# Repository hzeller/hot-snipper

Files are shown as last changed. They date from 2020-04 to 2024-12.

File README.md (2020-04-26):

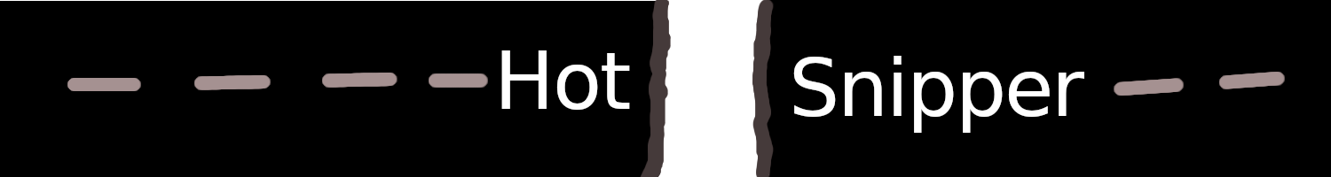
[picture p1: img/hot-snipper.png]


# Hot Knife cutting machine for synthetic button-hole bands

*Work in Progress*

Here at [MakerNexus], we're now producing the [Covid-19 effort][FaceShields]
face-shield parts via injection-molding, so now one bottleneck is to cut
enough elastic bands, which at this point happens entirely by hand.

This device helps to cut button-hole elastic.

It is specialized to work with the particular band we have in width
and button-hole distance; it cuts exactly the length we need (18 holes apart,
just between the holes). Changes in these specifications can easily be
adapted with the parametric CAD model.

This machine is for that, a hot knife (really at this point: hot wire) cutter
that allows to cut multiple parallel bands at once.

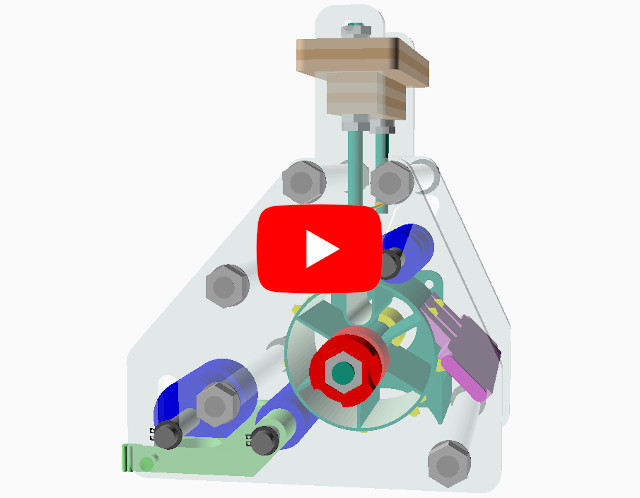
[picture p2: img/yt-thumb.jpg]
(https://www.youtube.com/watch?v=Wu0xrwdAlOw "Animation")


## Manufacturing
Most items can be entirely 3D printed, the side panels and wooden handle
is laser cut. To generate manufacturing outputs with OpenSCAD, type `make`.

### 3D printing
The provided fab/band-cutter-machine.3mf file contains a print layout that
provides all the parts needed to print a machine that can cut two bands in
parallel (This fits on an area small enough to be printed on a Prusa Mini).

#### Changing parallel bands
By default, the stack of bands that is cut in parallel is two, but that
can be changed with a parameter. A machine that can cut up to 5 bands in
parallel can fit on a Prusa MK3 bed.

```bash
make BAND_STACK=5  # to build the new artifacts; here we want 5 bands
cd fab/            # because prusa-slicer 3MF does not handle relative paths...
prusa-slicer band-cutter-machine.3mf
# Now, press F5 in the UI for reload.
```

There seems to be a bug in prusa-slicer which then slightly mis-aligns the
cylinder support enforcer around the main wheel; adjust that first before
slicing.

 Two band wide                      | Five band wide
------------------------------------|------------------------------------
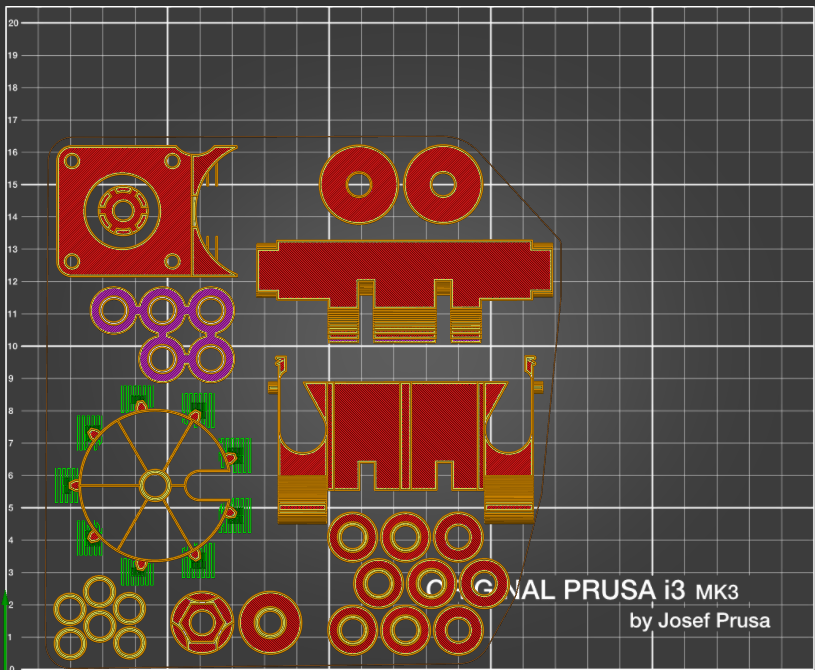
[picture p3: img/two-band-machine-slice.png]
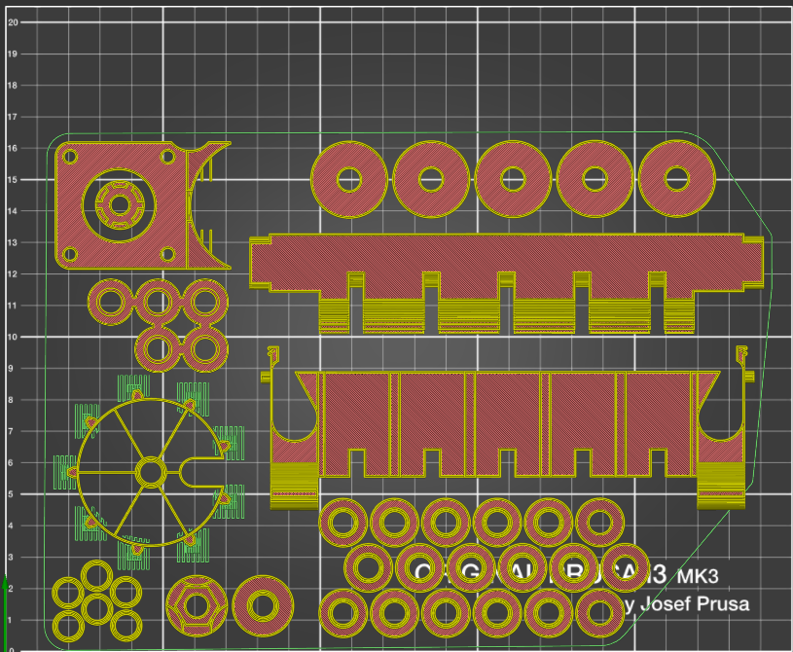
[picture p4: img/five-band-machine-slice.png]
 | 

The side-panels take a lot of time to print, so we laser-cut these (but
you can also print `fab/mount_panel.stl` if in a pinch and don't have access
to a laser cutter).

### Laser Cutting

There are two files, provided as DXF format that need to be laser-cut.

  * `fab/laser_cut_knife_slider.dxf` Needs to be cut from 3mm plywood.
  * `fab/laser_cut_mount_panel.dxf` can be wood, but ideally transparent
    acrylic to inspect the inside of the machine.

 Knife Slider (plywood, 3mm)        | Mount Panel (acrylic, 6mm)
------------------------------------|------------------------------------
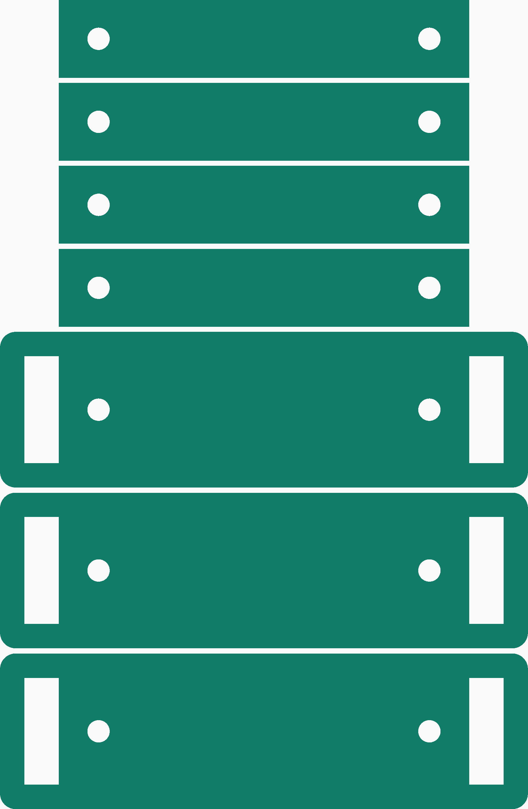
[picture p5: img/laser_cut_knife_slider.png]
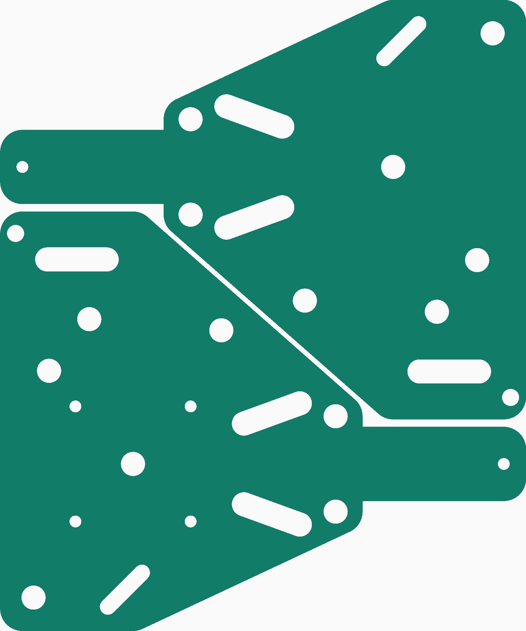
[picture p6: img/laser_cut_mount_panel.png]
 | 

## Assembly

Parts fit together pretty straightforward, check out the rendering and
picture below. Note that the spacing tubes for the axles come in two sizes:
the ones around the in-feed idler with the big wheels are slightly longer than
the other idler axes.

As 'axles', I am using easy-to-get threaded rods, cut to length (whatever
is easy to get; 6mm or 1/4").
All idler-axles should be held in place by retaining rings (I don't have any
right now, so this is why it is temporarily using nuts).

The center wheel is driven by a stepper motor, mounted on one side of the
panel. There is a meshing coupler that drives the wheel. Since the motor
axle is not long enough to go all the way through the machine, there is a
floating axle on the opposing side that is mounted firmly perpendicular to
the panel with flat nuts with a large surface.

The hot wire is mounted between two threaded rods (#8, about 4.2mm), held
apart by a wooden block made up of a couple of layers laser-cut plywood. That
way, that part does not soften over time near the rods that get warm in
operation.

Put aluminum sticky tape inside the wheel channel.

 Render                     | Assembled (older model)
----------------------------|-----------------------
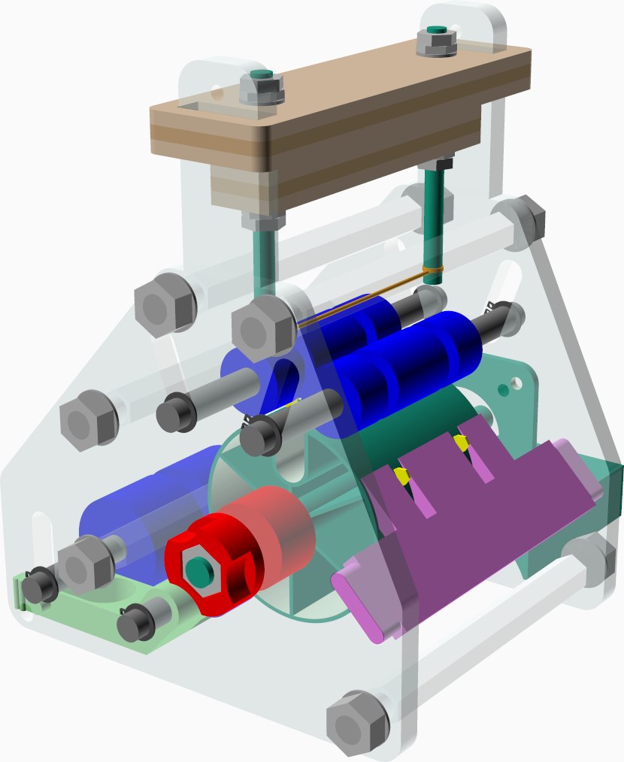
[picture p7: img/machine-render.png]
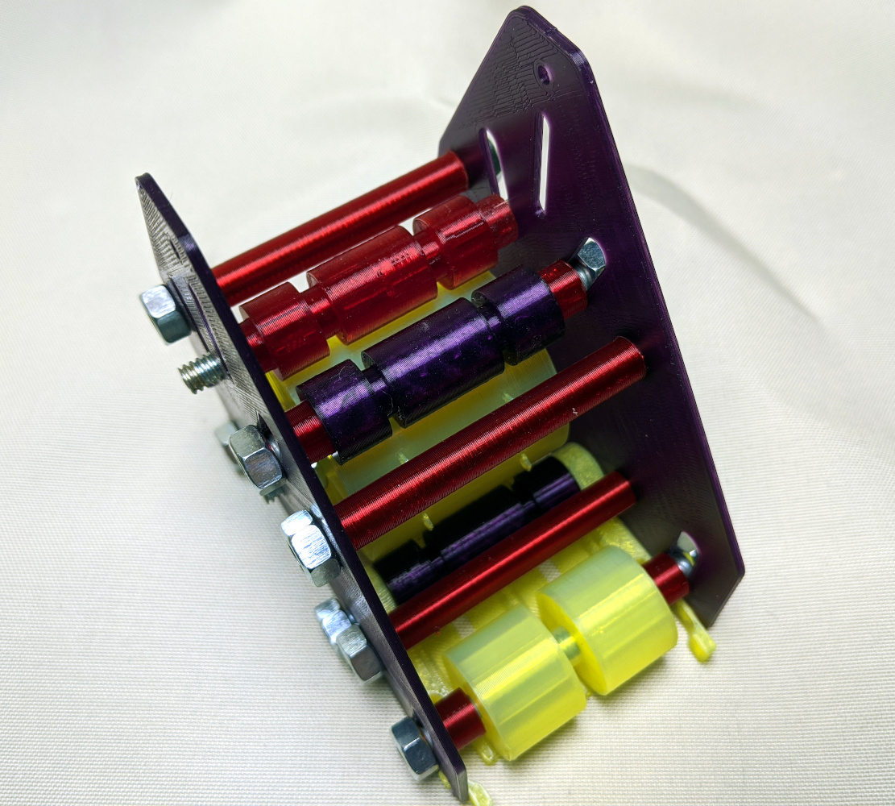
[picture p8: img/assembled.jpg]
 | 

## Usage

Loading the band requires it to go around the lower idler, then around the
central wheel and emerging at the top.

In order to get it through the in-feed tray and under the lower idler, it
is possible to unlatch the infeed-tray and rotate so that this can be done
with the least amount of fiddling.

 Feeding with opened loading tray        | Closed back up
-----------------------------------------|----------------
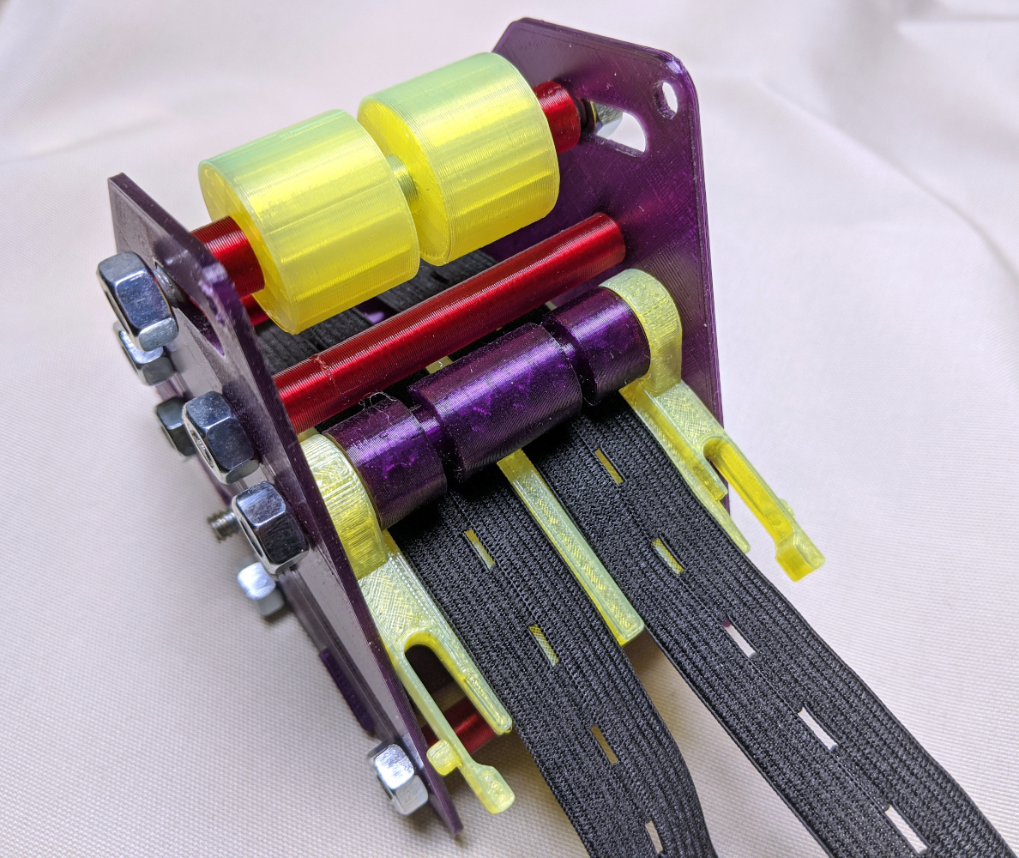
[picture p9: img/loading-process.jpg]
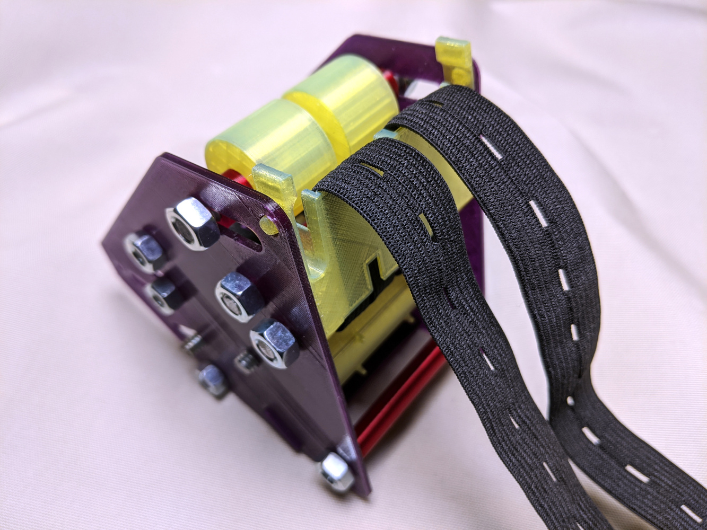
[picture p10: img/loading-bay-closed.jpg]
             | 

Now, wrap around the button elastic half way around the big wheel, then
under the top idlers (that can be moved up manually. In this picture purple
and red) so that the elastics emerge at the front; we're now fully loaded:

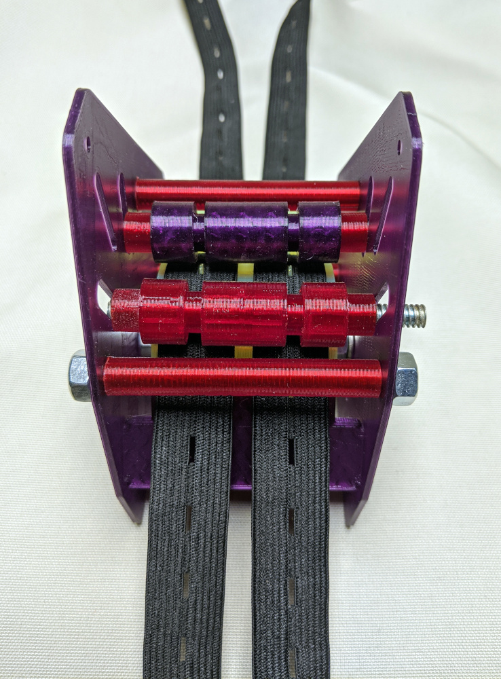
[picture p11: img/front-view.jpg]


### License

This is shared with the Creative Commons Attribution-ShareAlike [CC-BY-SA]
license.

[MakerNexus]: https://makernexus.com/
[FaceShields]: https://www.covidshieldnexus.org/
[CC-BY-SA]: https://creativecommons.org/licenses/by-sa/4.0/

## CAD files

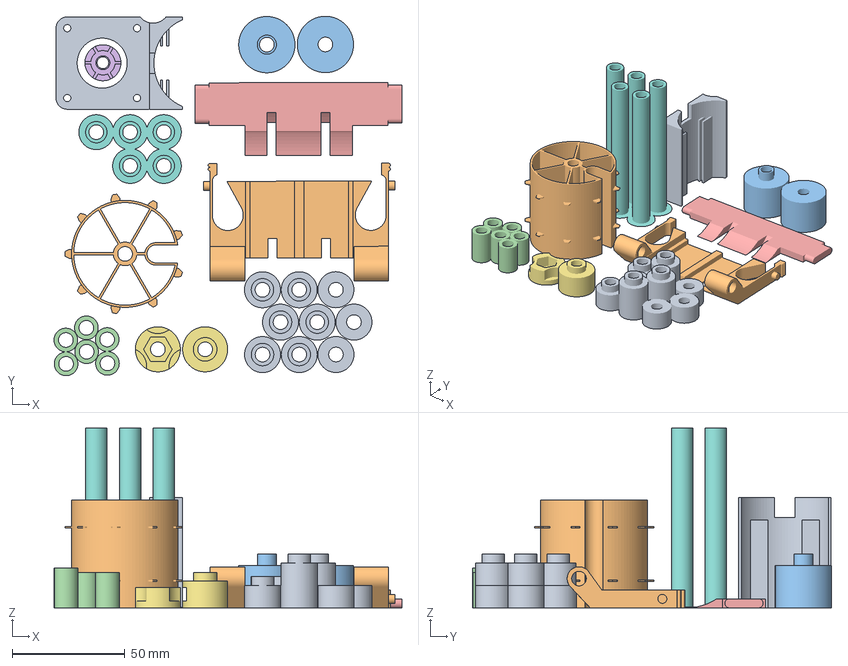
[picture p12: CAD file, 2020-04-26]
fab/band-cutter-machine.3mf
154.5 x 159.6 x 79.8 mm
print_wheel_idler.stl
infeed_fancy_tray.stl
print_infeed_weight_idler.stl
print_sidewall_clearance_distance_rings.stl
print_outfeed.stl
motor_coupler.stl
print_motor_bearing_parts.stl
print_stack_spacer.stl
print_nema_motor_stand.stl
wheel_stack.stl

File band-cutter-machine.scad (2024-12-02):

// -*- mode: scad; c-basic-offset: 2; indent-tabs-mode: nil; -*-
// (c) 2020 Henner Zeller <h.zeller@acm.org>
//
// This file is provided under the license condition of Creative Commons BY-SA
// https://creativecommons.org/licenses/by-sa/4.0/

use <utils.scad>

$fn=120;
e=0.01;
PI=3.1415926536;

stack=2;

// In one animation, we go through a few cycles, as we move camera positions,
// see camera_position() function.
anim_t=5*$t % 1;

// The phases we animate the knife and rotation.
anim_knife_range = [0, 0.6];  // first 60% of the time.
anim_rot_range = [0.6, 1];

//button_hole_distance=25.4 / 1.5;  // theoretical..
button_hole_distance=564 / 34;      // measured ...
hole_count=18;   // This determines the length of the final band. Must be even.

band_separation=4.1;               // How far apart we have the bands
baseline_band=19.8;                // Elastic band width.
band_thick=baseline_band + band_separation;  // Actual width + separation.

side_wall_clearance=16;           // Clearance mostly for the hot wire.
axle_dia=6.5;   // 1/4" rod + extra; we use that for all axles, main and idlers
axle_hex_flat_size=11;  // hex nut for above.
axle_hex_thick=6;

bands_per_wheel=0.5;
cut_slot_deep=10;

axle_display=axle_dia;
spoke_angle=60;

// Main wheel parameters
wheel_wall=1;
spoke_thick=1;
spoke_slot=4;

hole_angle=360/(bands_per_wheel*hole_count);
circ=bands_per_wheel * hole_count * button_hole_distance;
radius=circ / (2*PI);

idler_dia=16;
idler_cutout=4;
infeed_idler_dia=25;

knife_movement=25;     // Total vertical movement

stack_spacer_wall=1.5;       // od vs. id for stack spacer tubes.
stack_spacer_rod_dia=axle_dia;
stack_spacer_print_flat=true;   // make hexagon instead of round.

// the part engaging with the frame. This is multiple of 3mm as cut from
// plywood.
knife_slide_layers=7;
knife_slide_top_layers=3;
knife_slide_layer_thick=3;
knife_slide_len=knife_slide_layers * knife_slide_layer_thick;
knife_slide_top_len=knife_slide_top_layers * knife_slide_layer_thick;
knife_slide_rod_hole=4.3;   // The diameter threaded rod holding the wire.

knife_slider_above_wire=30;
knife_into_wheel=4;   // How deep we go into the slot. Mostly for animation
knife_slider_slot_w=20;
knife_slider_ring_support=5;       // Ring that wraps around slide dagger
knife_slider_bottom_block_w=15;    // Needs to support at least the nut diameter

fit_tolerance=0.3;                 // Tolerance of parts in contact.
slide_tolerance=fit_tolerance;     // Tolerance of parts sliding
rotation_clearance=fit_tolerance;  // Similar for rotational

infeed_tray_high=4;
outfeed_offset=0.65;       // Wheel to outfeed wedge.

nema_cutout=false;   // should we have a central cut-out for the nema17?

mount_panel_thickness=6;  // thickness of material for the frame, e.g. acrylic.
mount_panel_corner_r=6;

// Blades engaging with the button-holes
blade_h=3.5;
blade_w=0.7;
blade_l=4;

top_knife_pos = radius - knife_into_wheel
  + knife_slider_above_wire
  + (knife_slide_layers-knife_slide_top_layers)*knife_slide_layer_thick;

mount_hole_flush_with_top_knife
= top_knife_pos - axle_dia/2-stack_spacer_wall
  - 2.5;  // To accomodate washer and nut.
panel_corner_flush_with_top_knife = top_knife_pos - mount_panel_corner_r;

mount_hole_next_to_knife_block = knife_slider_bottom_block_w/2
  + stack_spacer_wall + stack_spacer_rod_dia/2
  + 2*slide_tolerance;  // a bit more than usual because we dive into it.

// Places where we add spacers to rigidly hold together the two side-frames.
mount_holes
 = [[39, -radius+12], [36, radius],  // Infeed side
    [-36, -radius-3],                // Outfeed side
    // Top around knife slider.
    [mount_hole_next_to_knife_block, mount_hole_flush_with_top_knife],
    [-mount_hole_next_to_knife_block, mount_hole_flush_with_top_knife]];

mount_panel_corners
 = [[-39, -radius - 6],         // bottom, out-feed side
    [-39, 0], //[-30, +radius+idler_dia], // up out-feed side.
    [-mount_hole_next_to_knife_block, panel_corner_flush_with_top_knife],
    [mount_hole_next_to_knife_block, panel_corner_flush_with_top_knife], // summit
    [62, 0], [62, -radius - 6]];  // down, in-feed

echo("circumreference ", circ, "; radius=", radius, "; teeth=", bands_per_wheel*hole_count, "; inner-width: ", stack * band_thick + 2*side_wall_clearance, "; knife-rod-distance: ", stack * band_thick + side_wall_clearance);

// Some colors used below
color_tooth="yellow";
color_knife="orange";   // glow
color_wheel_idler="blue";
color_axle="gray";
color_infeed="lightgreen";
color_outfeed="violet";
color_panel=[1, 1, 1, 0.1];
color_stack_spacer=[0, 1, 0, 0.25];
color_motor_coupler="yellow";
color_counter_bearing="red";
color_wood=["#d8c0a3", "#c9a77e"];  // plywood 'wood' layers

module mount_place(dia) {
  translate([0, 0, -band_thick/2]) cylinder(r=dia/2 + 2, h=band_thick);
}

module mount_place_punch(dia) {
  translate([0, 0, -(band_thick+e)/2]) cylinder(r=dia/2, h=band_thick+2*e);
}

// A 'tooth' engaging with a button hole.
module button_hole_tooth() {
  color(color_tooth) hull() {
    cube([e, blade_l, blade_w], center=true);
    translate([1.5, 0, 0]) cube([e, blade_l, blade_w], center=true);
    translate([blade_h, 0, 0]) cube([e, blade_l-2, blade_w], center=true);
  }
}

// Widening to accomodate hot knife through wheel.
module spoke_cut_widening(from_edge=cut_slot_deep) {
  widening_r=spoke_slot + spoke_thick;
  translate([radius - from_edge, 0, -band_thick/2]) hull() {
    cylinder(r=widening_r, h=band_thick);
    translate([from_edge, -widening_r, 0]) cube([e, 2*widening_r, band_thick]);
  }
}

module spoke_cut_widening_punch(from_edge=cut_slot_deep) {
  cutout_h=band_thick+2*e;
  translate([radius-from_edge, 0, -cutout_h/2]) hull() {
    cylinder(r=spoke_slot, h=cutout_h);
    translate([from_edge, -spoke_slot, 0]) cube([e, 2*spoke_slot, cutout_h]);
  }
}

module basic_wheel(extra=0) {
  // Outer cylinder, hollowed
  translate([0, 0, -band_thick/2]) difference() {
    cylinder(r=radius, h=band_thick);
    translate([0, 0, -e]) cylinder(r=radius-wheel_wall, h=band_thick+2*e);
  }

  // spokes.
  intersection() {
    union() {
      for (a=[0:spoke_angle:360]) {
        rotate([0, 0, a]) {
          translate([radius/2, 0, 0]) cube([radius, spoke_thick+extra, band_thick], center=true);
        }
      }
      spoke_cut_widening();
    }

    translate([0, 0, -band_thick/2]) cylinder(r=radius, h=band_thick);
  }

  mount_place(dia=axle_dia+extra);  // axle in center
}

module wheel_assembly(extra=0) {
  difference() {
    basic_wheel(extra);
    spoke_cut_widening_punch();
    mount_place_punch(dia=axle_dia-extra);
  }

  for (a=[hole_angle/2:hole_angle:360-e]) {
    rotate([0, 0, a]) translate([radius-0.5, 0, 0]) button_hole_tooth();
  }
}

module wheel_stack(layers=stack, with_axle=false) {
  d=band_thick;
  axle_extra=side_wall_clearance+mount_panel_thickness + 10;
  for (i = [0:1:layers-e]) {
    translate([0, 0, i*d]) wheel_assembly();
  }

  if (with_axle) {
    // TODO: add motor mount thing and counter-nut.
    translate([0, 0, -band_thick/2-axle_extra]) cylinder(r=axle_dia/2, h=layers*band_thick+2*axle_extra);
  }
}

// The knife is mostly non-3D printed, but made out of other materials
//  * the wire itself out of nichrome
//  * the connecting columns are some threaded rod.
module knife(s=stack) {
  d=band_thick;
  nd=8;   // nut dia
  nh=2.5; // nut height
  translate([-d/2, -0, 0]) {
    translate([-side_wall_clearance/2, 0, 0]) rotate([0, 90, 0]) color(color_knife)
      cylinder(r=0.5, h=s*d+side_wall_clearance);  // 'wire'

    translate([-side_wall_clearance/2, 0, 0]) {
      translate([0, 0, -3]) cylinder(r=4.5/2, h=60);  // rod
      color(color_knife) cylinder(r=5/2, h=1);
      translate([0, 0, knife_slider_above_wire-nh]) hex_nut(flat_dia=nd, h=nh);
      translate([0, 0, knife_slider_above_wire-2*nh]) rotate([0, 0, 17]) hex_nut(flat_dia=nd, h=nh); // counter nut.
      translate([0, 0, knife_slider_above_wire+knife_slide_len]) hex_nut(flat_dia=nd, h=nh, with_washer=true);
      translate([0, 0, knife_slider_above_wire+knife_slide_len+nh]) rotate([0, 0, 28]) hex_nut(flat_dia=nd, h=nh);
    }
    translate([s*d+side_wall_clearance/2, 0, 0]) {
      translate([0, 0, -3]) cylinder(r=4.5/2, h=60);
      color(color_knife) cylinder(r=5/2, h=1);
      translate([0, 0, knife_slider_above_wire-nh]) hex_nut(flat_dia=nd, h=nh);
      translate([0, 0, knife_slider_above_wire-2*nh]) rotate([0, 0, 38]) hex_nut(flat_dia=nd, h=nh); // counter nut.
      translate([0, 0, knife_slider_above_wire+knife_slide_len]) hex_nut(flat_dia=nd, h=nh, with_washer=true);
      translate([0, 0, knife_slider_above_wire+knife_slide_len+nh]) rotate([0, 0, 19]) hex_nut(flat_dia=nd, h=nh);
    }
    translate([0, 0, knife_slider_above_wire]) knife_slider();
  }
}
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

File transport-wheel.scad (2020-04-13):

// -*- mode: scad; c-basic-offset: 2; indent-tabs-mode: nil; -*-

$fn=96;
e=0.02;

PI=3.1415926536;

tray_idler_dia=20;

stack=2;
bands_per_wheel=0.5;
cut_slot_deep=10;
axle_dia=6.5;   // 1/4" rod + extra
axle_display=axle_dia - 0.5;
mount_hole_dia=4.5;
mount_hole_pos=5;  // from outside
spoke_angle=60;
do_screws=false;
do_spokes=true;
knife_idler_axle=5;

wheel_wall=1;
spoke_thick=1;

band_separation=1;
band_thick=19.5 + band_separation;
//band_center_thick=12;
band_center_thick=band_thick;


side_wall_clearance=6.95;

hole_count=18;   // This determines the length
hole_angle=360/(bands_per_wheel*hole_count);

//button_hole_distance=286/17;  // measured mm / hole count.
//button_hole_distance=594/35;  // measured mm / hole count.
button_hole_distance=25.4 / 1.5;  // probably actual value.
circ=bands_per_wheel * hole_count * button_hole_distance;
radius=circ / (2*PI);

blade_h=3.5;
blade_w=0.9;
blade_l=5;

mount_holes = [[-30, -radius-2], [30, -radius-2],
	       [30, radius+10], [-28, radius+5]];

echo("circumreference ", circ, "; radius=", radius, "; teeth=", bands_per_wheel*hole_count, "; inner-width: ", stack * band_thick + 2*side_wall_clearance);

module mount_place(dia=mount_hole_dia) {
  translate([0, 0, -band_thick/2]) cylinder(r=dia/2 + 2, h=band_thick);
}

module mount_place_punch(dia=mount_hole_dia) {
  translate([0, 0, -(band_thick+e)/2]) cylinder(r=dia/2, h=band_thick+2*e);
}

module hole_retainer() {
  color("yellow") hull() {
    cube([e, blade_l, blade_w], center=true);
    translate([1.5, 0, 0]) cube([e, blade_l, blade_w], center=true);
    translate([blade_h, 0, 0]) cube([e, blade_l-2, blade_w], center=true);
  }
}

module spoke_cut_widening(from_edge=cut_slot_deep) {
  widening_r=2 + spoke_thick;
  hull() {
    translate([radius - from_edge, 0, -band_thick/2]) cylinder(r=widening_r, h=band_thick);
    if (do_screws) {
      for (a = [-5, 5]) {
        rotate([0, 0, a]) translate([radius-mount_hole_pos, 0, 0]) mount_place();
      }
    } else {
      translate([radius, 0, -band_thick/2]) cylinder(r=widening_r, h=band_thick);
    }
  }
}

module spoke_cut_widening_punch(from_edge=cut_slot_deep) {
  translate([radius-from_edge, 0, -15]) hull() {
    cylinder(r=2, h=30);
    translate([50, 0, 0]) cylinder(r=2, h=30);
  }
}

module basic_wheel() {
  translate([0, 0, -band_center_thick/2]) difference() {
    cylinder(r=radius, h=band_center_thick);
    translate([0, 0, -e]) cylinder(r=radius-wheel_wall, h=band_center_thick+2*e);
  }

  intersection() {
    translate([0, 0, -band_thick/2]) difference() {
      cylinder(r=radius, h=band_thick);
      translate([0, 0, -e]) cylinder(r=radius-wheel_wall, h=band_thick+2*e);
    }
    union() {
      support_arc(0, 30, radius=radius+10, high=band_thick);
      if (bands_per_wheel==2)
        support_arc(180, 30, radius=radius+10, high=band_thick);
    }
  }

  // spokes.
  intersection() {
    union() {
      for (a=[0:spoke_angle:360]) {
        rotate([0, 0, a]) {
          if (do_spokes) translate([radius/2, 0, 0]) cube([radius, spoke_thick, band_center_thick], center=true);
        }
      }

      spoke_cut_widening();

      // Spoke mounts
      if (do_screws) {
        for (a=[spoke_angle:spoke_angle:179]) {
          rotate([0, 0, a]) translate([radius-mount_hole_pos, 0, 0]) mount_place();
          rotate([0, 0, -a]) translate([radius-mount_hole_pos, 0, 0]) mount_place();
        }

        for (a = [-5, 5, 175, 185]) {
          rotate([0, 0, a]) translate([radius-mount_hole_pos, 0, 0]) mount_place();
        }
      }

    }

    translate([0, 0, -band_thick/2]) cylinder(r=radius, h=band_thick);
  }

  if (do_spokes) mount_place(dia=axle_dia);  // axle in center
}

module wheel_assembly() {
  difference() {
    basic_wheel();
    spoke_cut_widening_punch();
    if (do_screws) {
      for (a=[spoke_angle:spoke_angle:179]) {
        rotate([0, 0, a]) translate([radius-mount_hole_pos, 0, 0]) mount_place_punch();
        rotate([0, 0, -a]) translate([radius-mount_hole_pos, 0, 0]) mount_place_punch();
      }
      for (a = [-5, 5, 175, 185]) {
        rotate([0, 0, a]) translate([radius-mount_hole_pos, 0, 0]) mount_place_punch();
      }
    }
    mount_place_punch(dia=axle_dia);
  }

  for (a=[hole_angle/2:hole_angle:360-e]) {
    rotate([0, 0, a]) translate([radius-0.5, 0, 0]) hole_retainer();
  }
}

module stack(layers=3, with_axle=true) {
  d=band_thick;
  axle_extra=side_wall_clearance + 10;
  for (i = [0:1:layers-e]) {
    translate([0, 0, i*d]) wheel_assembly();
  }
  if (with_axle) {
    translate([0, 0, -band_thick/2-axle_extra]) cylinder(r=axle_dia/2, h=layers*band_thick+2*axle_extra);
  }
}

module knife(layers=3, anim_stage=0) {
  movement=15;
  side=0;
  down=sin(anim_stage*180) * movement;
  d=band_thick;
  translate([-side-d/2, -0.5, radius+10-down]) color("red") cube([layers*d+(2*side), 1, 30]);
}

module anim(s=4) {
  t=$t;
  rotate([0, 0, 0]) {
    rotate([180 + ((t < 0.8) ? (t/0.8) * 720 : 0), 0, 0]) rotate([0, 90, 0]) stack(s);
    knife(s, anim_stage = (t > 0.8) ? (t-0.8)/0.2 : 0);

    rotate([90, 0, 180]) rotate([0, -90, 0]) color("darkgray") tangential_band(r=radius, band_wide=band_thick-band_separation-1, in_angle=45, out_angle=135, total_len=500, start_len=481.5-t*button_hole_distance*hole_count);
  }
}

//wheel_assembly();
//stack(1);

module arc_range(start=-10, end=10, radius=100, high=5) {
  hull() {
    cylinder(r=e, h=high);
    rotate([0, 0, start]) translate([radius, 0, 0]) cylinder(r=e, h=high);
    rotate([0, 0, end]) translate([radius, 0, 0]) cylinder(r=e, h=high);
  }
}

module support_arc(center=0, angle_dist=10, radius=100, high=10) {
  small_dist=angle_dist/3;
  hull() {
    translate([0, 0, high/2]) arc_range(start=center-small_dist, end=center+small_dist, radius=radius, high=e);
    arc_range(start=center-angle_dist, end=center+angle_dist, radius=radius, high=e);
    translate([0, 0, -high/2]) arc_range(start=center-small_dist, end=center+small_dist, radius=radius, high=e);
  }
}

//stack(2);

module knife_idler(is_first=false, is_last=false) {
  center_free=3;
  outer=8;
  big_part=(is_first || is_last)
    ? (band_thick-center_free)/2
    : (band_thick-center_free);
  difference() {
    union() {
      cylinder(r=outer, h=big_part);
      if (!is_last) cylinder(r=outer-3, h=big_part+center_free);
    }
    translate([0, 0, -e]) cylinder(r=axle_dia/2, h=band_thick+2*e);
  }
}

module knife_idler_stack(s=5, print_distance=-1, with_axle=false, gravity_holes=false) {
  d = band_thick;
  color("blue") for (i = [0:1:s+1-e]) {
    is_first=(i == 0);
    is_last = (i == s);
    if (print_distance < 0) {
      translate([0, 0, is_first ? 0 : (i-0.5)*d+1.5])
        knife_idler(is_first=is_first, is_last=is_last);
    } else {
      translate([i*print_distance, 0, 0])
        knife_idler(is_first=is_first, is_last=is_last);
    }
  }
  axle_extra=side_wall_clearance + 10;
  if (with_axle) {
    color("gray") translate([0, 0, -axle_extra]) cylinder(r=axle_display/2, h=s*d+2*axle_extra);
  }
  if (gravity_holes) {
    hull() {
      translate([1, 0, -axle_extra]) cylinder(r=axle_dia/2, h=s*d+2*axle_extra);
      translate([-15, 0, -axle_extra]) cylinder(r=axle_dia/2, h=s*d+2*axle_extra);
    }
  }
}

module band_tray(s=5, len=40, extra=0) {
  color("silver") for (i = [0:1:s-e]) {
    translate([i*band_thick, 0, 0]) {
      cube([band_thick, len, 1]);
      cube([band_separation/2, len, 4]);
      translate([band_thick-band_separation/2, 0, 0])
        cube([band_separation/2+e, len, 4]);
    }
  }
  slot_w=20;
  sw_r=4/2 + extra;
  sw=side_wall_clearance+4;
  translate([-sw, 0, 0]) hull() {
    translate([0, 10, 4/2]) rotate([0, 90, 0]) cylinder(r=sw_r, h=sw);
    translate([0, 10+slot_w, 4/2]) rotate([0, 90, 0]) cylinder(r=sw_r, h=sw);
  }
  translate([s*band_thick, 0, 0]) hull() {
    translate([0, 10, 4/2]) rotate([0, 90, 0]) cylinder(r=sw_r, h=sw);
    translate([0, 10+slot_w, 4/2]) rotate([0, 90, 0]) cylinder(r=sw_r, h=sw);
  }

  translate([-side_wall_clearance, 10/2, 0]) cube([side_wall_clearance, 30, 4]);
  translate([s*band_thick, 10/2, 0]) cube([side_wall_clearance, 30, 4]);
}

module tray_idler(outer=15) {
  difference() {
    union() {
      cylinder(r=outer, h=band_thick-band_separation-1);
      cylinder(r=outer-5, h=band_thick);
    }
    translate([0, 0, -e]) cylinder(r=axle_dia/2, h=band_thick+2*e);
  }
}
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

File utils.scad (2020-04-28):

// -*- mode: scad; c-basic-offset: 2; indent-tabs-mode: nil; -*-
// (c) 2020 Henner Zeller <h.zeller@acm.org>
//
// This file is provided under the license condition of Creative Commons BY-SA
// https://creativecommons.org/licenses/by-sa/4.0/

e=0.01;
fit_tolerance=0.3;                 // Tolerance of parts in contact.

// Scales range between 0..1 to from..to
function scale_range(t, from, to) = t * (to - from) + from;

// If t falls within the scene_start...scene_end range, scale linearly
// between these and return 0..1. if t < scene_start, return 0,
// if t > scene_end, return 1
function anim_phase(t, scene_range = [0, 1])
  = ((t < scene_range[0]) ? 0.0
     : (t >= scene_range[1] ? 1.0
        : (t - scene_range[0])/(scene_range[1] - scene_range[0])));

// Returns an S-curve animation range between 0..1 (just a piece of cos())
function smooth_anim(t) = (-cos(t*180) + 1)/2;

function in_interval(x, from, to) = (x >= from && x < to);

// Model a hex nut with the distance between the flat faces of flat_dia.
// If channel_len is given, provides a sideways channel.
module hex_nut(flat_dia, h, channel_len=-1,
               with_washer=false, washer_thick=0.7,
               show_screw_dia=-1) {
  r = flat_dia / cos(30) / 2;
  color("silver") cylinder(r=r, h=h, $fn=6);
  if (show_screw_dia > 0) color("darkgray") cylinder(r=show_screw_dia/2, h=h+e);
  if (with_washer) color("darkgray") cylinder(r=r, h=washer_thick);
  if (channel_len > 0) {
    translate([0, -flat_dia/2, 0]) cube([channel_len, flat_dia, h]);
  }
}

module rounded_cube(d=[10,10,10], center=false, r=3) {
     translate([center ? -d[0]/2 : 0,
		center ? -d[1]/2 : 0,
		center ? -d[2]/2 : 0]) hull() {
	  translate([r, r, 0]) cylinder(r=r, h=d[2]);
	  translate([d[0] - r, r, 0]) cylinder(r=r, h=d[2]);
	  translate([r, d[1]-r, 0]) cylinder(r=r, h=d[2]);
	  translate([d[0]-r, d[1]-r, 0]) cylinder(r=r, h=d[2]);
     }
}

// m3_screw space occupied by a M3 screw with optional nut and
// nut-access channel. Screw is centered around the Z-axis, with the
// screw in the positive and screw-head in the negative range.
// nut_at: start of where a m3 nut shoud be placed. -1 for off.
// nut_channel: make a channel of given length to slide a nut in.
//              nut channel extends in negative Y direction. Rotate as needed.
module m3_screw(len=60, nut_at=-1, nut_channel=-1) {
  m3_dia=3.4;         // Let it a little loose to not overconstrain things.
  m3_head_dia=6;
  m3_head_len=3;
  m3_nut_flat_dia=5.4 + 2*fit_tolerance;
  m3_nut_dia=5.4 / cos(30) + 2*fit_tolerance;  // /= cos(30) for circumcircle
  m3_nut_thick=2.8;

  cylinder(r=m3_dia/2, h=len);
  translate([0, 0, -20+e]) cylinder(r=m3_head_dia/2, h=20);
  if (nut_at >= 0) {
    translate([0, 0, nut_at]) {
      rotate([0, 0, -90]) hex_nut(flat_dia=m3_nut_flat_dia, h=m3_nut_thick,
        channel_len=nut_channel);
    }
  }
}

module retainer_clip(r=5, h=0.5) {
  width=1.2;
  gap=0.4;
  color("#505050") translate([0, 0, -h/2]) difference() {
    union() {
      cylinder(r=r+width, h=h);
      translate([-(3*width)/2, 0, 0]) cube([3*width, r+2*width, h]);
    }
    translate([0, 0, -e]) {
      cylinder(r=r, h=h+2*e);
      translate([-gap, 0, 0]) cube([2*gap, r+2*width+e, h+2*e]);
      translate([+(width-gap/2), r+1.3*width, 0]) cylinder(r=0.5, h=h+2*e);
      translate([-(width-gap/2), r+1.3*width, 0]) cylinder(r=0.5, h=h+2*e);
    }
  }
}

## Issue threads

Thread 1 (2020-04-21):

Needs: added sensor for detecthing if we reached the notch

hzeller, 2020-04-21:
If the current on the stepper is too low, it might be that there are lost steps when it needs to pull hard on incoming bands. There should be a secondary test to make sure that is the case, e.g. a fork light barrier. When at the end of a cycle, we have not reached the notch yet, it keeps turning until it is; possibly recording how often this happens and store in firmware for later adjustment of current.

Also: this can be used to auto-align the wheel when the motor is switched on.

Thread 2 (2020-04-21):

Temperature controlled knife.

hzeller, 2020-04-21:
Right now, we have a hot wire that melts through the plastic. The wire is fairly low thermal mass, which means it cools down quickly when going through the material, and also requires changes e.g when there is a breeze due to working outside or a fan.

So instead of a simple wire, we should heat a flat piece of metal with a wire on it and a temperature sensor. The wire can be curled to work with common 12V supplies, so that we can have a single power supply with fairly low current to run it.

Maybe a copper plate sandwiched between two aluminum plates heated with wires on both sides (insulated with e.g. Capton ); ` ⌇` represents the heating wire layer here:
```
|⌇|⌇|   <-  AL-capton-heating-capton-CU-capton-heating-capton-AL
|⌇|⌇|
  |     <- CU (copper)
```

Temperature sensor is cemented in a central place.

The control circuit could actually be a re-purposed 3D printer board, which already has temperature sensor input.

Advantages: independent of airflow conditions, less heat-related expansion bending of wire; also we can control the temperature to exactly melting and not burning.

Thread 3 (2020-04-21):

Make it easier to replace knife: change mounting of knife.

hzeller, 2020-04-21:
Right now, the knife is locked into place between two slides poking out from the inside of the device.

Turns out, this makes it really hard to inspect, adjust, etc. the knife, as it requires to loosen the whole assembly to be wide enough to pull it out.

Instead, the top part of the outer frame should have parallel edges, and the wooden knife slider 'hugs around' this area. This makes it easy to just pull up the whole assembly with minimal issues.

It will also solve the current problem of it jamming when not pressed down very straight, as it will now have a much larger support area preventing this.

hzeller, 2020-04-23:
Fixed in a4f6660135f7299660de506ea8292d0c25ae794a

Closed 2020-04-23.

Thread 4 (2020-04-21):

Spring-loaded slack pick-up of temp expansion. Bottom support of hot wire.

hzeller, 2020-04-21:
to get more force on the wire, in particular when it expands, we should not directly mount it to the rods, but have a strong spring pulling it - when it expands due to temperature increase, it will then be still be taut.

For this, we will experience more bending force on the threaded rod holding it. So maybe extend the thraded rods and have a similar wooden spacer at the bottom of the machine to make the whole set-up more stiff. This has some issues w.r.t. placement of the rod though, as it can't be centered anymore as it would hit the main wheel axle. So it needs to be two parallel rods. Might get complicated; this might also be a non-issue if we had a temperature controlled knife (#2), so maybe we should focus on that,as needed anyway.

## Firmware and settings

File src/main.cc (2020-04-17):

// -*- mode: c++; c-basic-offset: 2; indent-tabs-mode: nil; -*-
//
// Super simple: on click, turn motor twice.

#include <avr/io.h>
#include <util/delay.h>
#include <stdint.h>

// Port D
#define BUTTON_BIT (1<<5)
#define ENABLE_SENSE (1<<3)

// Port B
#define STEP_BIT  (1<<4)
#define LED_RED   (1<<0)
#define LED_GREEN (1<<1)
#define LED_BLUE  (1<<2)

static constexpr int kFullCycle = 2;  // Each step is two delays for |¯|_|
static constexpr int kMicroSteps = 8;
static constexpr uint16_t kMaxStepSpeed = kMicroSteps * 400 * kFullCycle;

// Keep track of button release before next clicked() event is triggered.
// Also: debounce. (Hard-coded on PORTD, bit BUTTON_BIT)
class Button {
  // Let's make the debouncing fairly large as we might expect a foot switch
  // be connected with unknown specs.
  // But not too long to create an annoying lag.
  static constexpr uint16_t kDebounceWait = 30000;

public:
  Button() { PORTD |= BUTTON_BIT; /* pullup */}

  bool clicked() {
    const bool current_pressed = (PIND & BUTTON_BIT) == 0;  // neg. logic
    if (last_debounce_state_ != current_pressed) debounce_counter_ = 0;
    last_debounce_state_ = current_pressed;
    debounce_counter_++;
    if (debounce_counter_ < kDebounceWait)
      return false;
    const bool before = previous_pressed_;
    previous_pressed_ = current_pressed;
    return (current_pressed && !before);
  }

private:
  bool last_debounce_state_ = false;
  uint16_t debounce_counter_ = 0;
  bool previous_pressed_ = false;
};

// Not doing a trapezoidal acceleration motion profile yet, just starting
// slower, then linearly change delay time.
class MotionProfile {
  static constexpr int kCyclesPerDelay = 5;
  static constexpr int kSlowFactor = 5;
  static constexpr int kAccelerationJumps = 1;

  typedef uint16_t delay_t;

public:
  MotionProfile(uint16_t steps, uint16_t steps_per_second)
    : stage_(Stage::INIT), remaining_steps_(steps) {
    SetStepsPerSecond(steps_per_second);
  }

  // Setting speed is also allowed during the operation to allow adjustments.
  void SetStepsPerSecond(uint16_t steps_per_second) {
    target_speed_delay_ = F_CPU / kCyclesPerDelay / steps_per_second;
    start_ramp_delay_ = kSlowFactor * target_speed_delay_;
    accel_steps_ = (start_ramp_delay_ - target_speed_delay_)
      / kAccelerationJumps;
    switch (stage_) {
    case Stage::INIT: current_delay_ = start_ramp_delay_; break;
    case Stage::MOVING: current_delay_ = target_speed_delay_; break;
    default:
      ;
      // We don't mess with current acceleration phases.
    }
  }

  bool has_more() const { return remaining_steps_ > 0; }
  void delay() {
    switch (stage_) {
    case Stage::INIT:
    case Stage::ACCELERATION:
      current_delay_ -= kAccelerationJumps;
      if (current_delay_ <= target_speed_delay_) {
        current_delay_ = target_speed_delay_;
        stage_ = Stage::MOVING;
      } else {
        stage_ = Stage::ACCELERATION;
      }
      break;

    case Stage::MOVING:
      current_delay_ = target_speed_delay_;
      if (remaining_steps_ <= accel_steps_) {
        stage_ = Stage::DECELERATION;
      }
      break;

    case Stage::DECELERATION:
      current_delay_ += kAccelerationJumps;
      if (current_delay_ > start_ramp_delay_)
        current_delay_ = start_ramp_delay_;
      break;
    }

    for (delay_t i = 0; i < current_delay_; ++i)
      asm("");  // prevent optimizing away
    remaining_steps_--;
  }

private:
  enum class Stage {
    INIT,
    ACCELERATION,
    MOVING,
    DECELERATION
  } stage_;

  uint16_t remaining_steps_;
  uint16_t accel_steps_;       // Steps the (ac-/de)celeration phase takes
  delay_t target_speed_delay_; // Speed for normal movement.
  delay_t start_ramp_delay_;   // Targeted speed at start of ramp.

  delay_t current_delay_;      // current delay, changing on circumstances
};

void send_steps(uint16_t steps) {
  MotionProfile step_gen(kMicroSteps*steps*2, kMaxStepSpeed);

  while (step_gen.has_more()) {
    PORTB ^= STEP_BIT;
    step_gen.delay();
  }
}

int main() {
  DDRB = STEP_BIT | LED_RED | LED_GREEN | LED_BLUE;
  PORTB |= LED_RED | LED_GREEN | LED_BLUE;  // Negative logic.

  Button button;
  for (;;) {
    if (button.clicked()) {
      if (PIND & ENABLE_SENSE) {  // Motor enable still off.
        PORTB &= ~LED_RED;
        _delay_ms(10);
        PORTB |= LED_RED;
      } else {
        PORTB &= ~LED_GREEN;
        send_steps(400);
        PORTB |= LED_GREEN;
      }
    }
  }
}

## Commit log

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2020-04-13 Add shoulders to in-feeds and out-feeds to properly space between the walls.
    [transport-wheel.scad]
2020-04-13 use indentation of 2.
    [transport-wheel.scad]
2020-04-13 Make sure out-feed has enough material removed around teeth. Side panel: improve readability by puttin corners in array.
    [band-cutter-machine.scad]
2020-04-13 More engagement with main wheel.
    [band-cutter-machine.scad]
2020-04-13 Not using screws anymore to stack wheels.
    [band-cutter-machine.scad]
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2020-04-13 Remove tangent band for now (needs to be adapted to roll around multiple wheels) consistent naming of outfeed.
    [band-cutter-machine.scad]
2020-04-14 some variable naming cleanup.
    [band-cutter-machine.scad]
2020-04-14 Make a 'snap lock' for the infeed tray.
    [band-cutter-machine.scad]
2020-04-14 Stiffen up snap
    [band-cutter-machine.scad]
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2020-04-14 A bit more packing, so that we can fit machines with 2 up to 5 bands on one build-plate
    [band-cutter-machine.3mf, band-cutter-machine.scad]
2020-04-14 Add images and a basic README.
    [band-cutter-machine.scad]
2020-04-14 Adapt distance of button holes to actual measured size.
    incoming roller: don't do extension on last roll.
    [band-cutter-machine.scad]
2020-04-14 Fix idler cutout parameter propagation.
    [band-cutter-machine.scad]
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2020-04-15 Slicer can't deal with keeping alignment of part and support enforcer. .. Replace with fresh version.
    [band-cutter-machine.3mf]
2020-04-15 More experiments with aligning support enforcer, but mostly looks like bug in slicer.
    [band-cutter-machine.3mf]
2020-04-15 Add side wall distance rolls. Should at some point be part of the design directly, now let's have separate rolls for easier assembly experiments.
    [band-cutter-machine.3mf, band-cutter-machine.scad]
2020-04-15 Always create mounting holes for motor for now, but not the nema central cutout.
    [band-cutter-machine.3mf, band-cutter-machine.scad]
2020-04-15 Take clearance into account for things that rotate.
    [band-cutter-machine.scad]
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2020-04-15 opening tray snap lock: add a little knurly thing to hold on to.
    [band-cutter-machine.3mf, band-cutter-machine.scad]
2020-04-15 Add a stand for a stepper motor.
    [band-cutter-machine.scad]
2020-04-15 Adapt motor sizes; add cable management.
    [band-cutter-machine.scad]
2020-04-15 Leave animation related functionality out of knife module.
    [band-cutter-machine.scad]
2020-04-16 Start visualizing hot wire better. Add more side-distance for knife to operate.
    [band-cutter-machine.scad]
2020-04-16 Add a motor coupler.
    [band-cutter-machine.scad]
2020-04-17 Add some axle support to be perpendicular to side-frame (the axle that is opposing the motor and only supported by the frame)
    [band-cutter-machine.scad]
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2020-04-18 Add a knife slider bar, holding the rods that spans the wire.
    The rods are simple threaded rod. The bar will be laser-cut from
    plywood (15mm: 5x 3mm), so that it is not susceptible to softening
    due to warmth over time.
    Had to increase the headroom to have enough distance to the idler
    wheels, enough slider engagement to not rock back and forth and
    enough distance between wire and handle-bar to have enough temperature
    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
    [band-cutter-machine.scad]
2020-04-18 Add DXF output to laser-cut hot-wire handle.
    [band-cutter-machine.scad]
2020-04-18 Move mounting screws around idlers up a little for easier access.
    In the course of that, the panel shape needed to be changed. To
    have that a little easier to edit, move that array containing the
    corners near array containing the mounting holes.
    [band-cutter-machine.scad]
2020-04-18 Adapt axle length and outfeed retainer to frame thickness.
    [band-cutter-machine.scad]
2020-04-18 Eliminate dual use of 'wheel_stack'.
    One is a module showing the wheel stack. The other was often used
    as local variable describing the stack thickness. In other places
    we commonly use 's' for that. Changed.
    [band-cutter-machine.scad]
2020-04-18 Add motor coupler and oposing nut to full assembly visualization.
    [band-cutter-machine.scad]
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2020-04-18 mount panel DXF: two versions, one with, one wihtout motor.
    Update README.
    [band-cutter-machine.scad]
2020-04-18 Right amount of clearance rings. Add manual 'brim' for stack spacer.
    [band-cutter-machine.scad]
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2020-04-22 Move the sliding meachnism outwards so that it is simple to remove and inspect knife without disassembling unit.
    [band-cutter-machine.scad]
2020-04-23 Make the lower knife block be slide-supported by the stack-spacers it passes through.
    [band-cutter-machine.scad]
2020-04-25 Make rounded knife slider. Move some smallish things into util.scad
    [band-cutter-machine.scad, utils.scad]
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2020-04-25 Make a little cutout for the motor stand to accomodate axle mounting that is right next to it.
    [band-cutter-machine.scad]
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2020-04-25 Add a cycle at the end with no camera movement.
    [band-cutter-machine.scad]
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2020-04-25 Don't create motor mount holes on opposing frame Also: No camera animation by default, otherwise it resets after each edit.
    [band-cutter-machine.scad]
2020-04-25 Fix some rendering artifacts o the motor coupler was color bleeding into the wheel. Have to render() first. o the outfeed tray was not properly punching through the frame. Add epsilon. o some obsolet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
    [band-cutter-machine.scad]
2020-04-25 Snap lock: add proper fit-tolerance to outside wall.
    Also: give it a distinctive color.
    [band-cutter-machine.scad]
2020-04-25 Make sure we end up at same place as start of animation.
    [band-cutter-machine.scad]
2020-04-25 Fix sloppy spoke_cut implementation, resulting in visible artifacts.
    [band-cutter-machine.scad]
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2020-04-25 Fix smooth animation for last segment.
    [band-cutter-machine.scad]
2020-04-25 Fix typo.
    [band-cutter-machine.scad]
2020-04-26 Update 3mf: include motor mount; make 2-band machine fit on Prusa Mini.
    [band-cutter-machine.3mf, band-cutter-machine.scad]
2020-04-26 Fix angle of infeed idlers on print bed.
    [band-cutter-machine.3mf]
2020-04-26 Provide an option to print stack spacers flat.
    In particular for larger machines, printing them upright is not
    a very stable idea.
    [band-cutter-machine.scad]
2020-04-26 Move bottom spacer rod further out to easier access main wheel.
    [band-cutter-machine.scad]
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2020-04-28 Formulate animation range with an array. Makes it easier to hand around.
    [band-cutter-machine.scad, utils.scad]
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2024-11-29 Fix indentation.
    [band-cutter-machine.scad]
2024-12-02 Create animation from Makefile.
    For that, set $vpt, $vpd and $vpf
    [band-cutter-machine.scad]
